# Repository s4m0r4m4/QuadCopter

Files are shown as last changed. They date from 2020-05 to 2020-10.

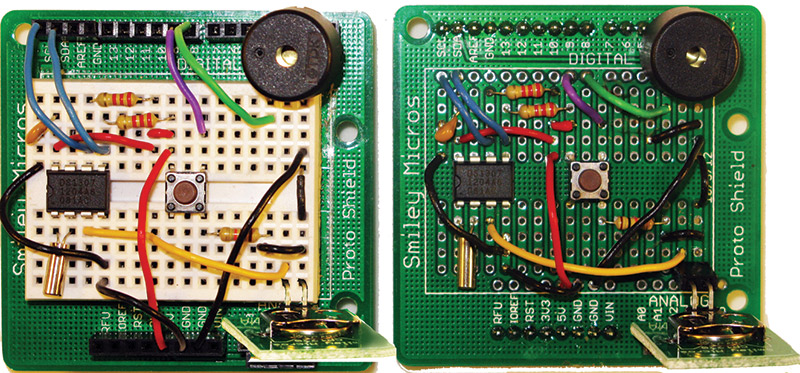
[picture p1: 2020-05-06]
Docs/How to solder.jpg

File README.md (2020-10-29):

# Overview
A simple quadcopter hobby project, build from scratch in terms of both software and hardware.

# Suggested Software Setup
1) Download VS code
2) Install the PlatformIO extension (you can try to beta Arduino Extension, but you will probably have library linking issues)
3) You'll have to install the "Servo" and "SD" libraries using the PlatformIO Extension (use the library panel)
4) It should build!

# Hardware Setup
## MPU-9250
 - VCC ---------------------- 3.3V
 - SDA ----------------------- A4
 - SCL ----------------------- A5
 - GND ---------------------- GND
 - 10 kOhm resistor from 3.3V to SDA
 - 10 kOhm resistor from 3.3V to SCL

Uses code from kriswiner/MPU9250 to read accelerometers, magnetometer, and gyroscopes from MPU9250 and then runs [Magdwick](https://www.x-io.co.uk/res/doc/madgwick_internal_report.pdf) (or Mahoney, depending on how I'm feeling) state estimation algorithm. Big thanks to Kris for his work there.
 
 ## Radio (FlySky FS-CT6) Setup
  TODO: Show pic
  
## Emax MT1806-2280KV Motors:
- https://www.banggood.com/EMAX-MT1806-KV2280-Brushless-Motor-For-Multirotor-p-933931.html?ID=521309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
- Max Trust: 360-460g (depending on propeller)
-	No. of cell: 2-3S
-	Framework: 12N14P
-	Propeller: 5" ~ 6"
-	Length: 26.7mm
-	Shaft: 2mm
- Motor Casing	Diameter: 23mm
-	Weight: 18g

## Battery: 
- http://www.getfpv.com/lumenier-1500mah-3s-45c-lipo-battery.html 
-	Length	88 mm
-	Width	35 mm
-	Height	22 mm
-	Weight	125g
-	C-Rating	45c - Burst 90c
-	Voltage	3s, 11.1v
-	Connector	XT60

## MicroSD Card Reader
- MicroSD card reader for Arduino Uno: https://www.amazon.com/gp/product/B07BJ2P6X6/ref=ppx_yo_dt_b_asin_title_o05_s00?ie=UTF8&psc=1
- MicroSD Card w/ SD-card adapter: https://www.amazon.com/gp/product/B07YLYX4NL/ref=ppx_yo_dt_b_asin_title_o04_s00?ie=UTF8&psc=1
- You can include an SD card reader if you chose to store data while flying (which is a good idea!)
- Since the SD card require a lot of data transfer, you'll get the best performance when connected up to the hardware SPI pins on the Arduino Uno: digital 13 (SCK), 12 (MISO) and 11 (MOSI). You will also need a fourth pin for the 'chip/secondary select' (SS) line. 

## Other Components:
- 5030 propellers: https://www.amazon.com/gp/product/B00Y4QNSFA/ref=oh_aui_detailpage_o00_s01?ie=UTF8&psc=1 
- Arduino Uno R3 (third-party brands are fine too): https://www.amazon.com/gp/product/B00P2FX9WY/ref=oh_aui_detailpage_o00_s03?ie=UTF8&psc=1 
- Frame: FCMODEL X4 M280L Wheelbase Glass Fiber Across Mini Quadcopter Frame Kit DIY RC Multicopter FPV Drone: https://www.amazon.com/gp/product/B014KNMKF0/ref=oh_aui_detailpage_o04_s00?ie=UTF8&psc=1
- Support Legs: https://www.amazon.com/gp/product/B00QHVVKEG/ref=ox_sc_sfl_title_1?ie=UTF8&psc=1&smid=A3Y26MC43SQCQ 
- MPU9250: https://www.amazon.com/Mpu-9250-Nine-axis-Attitude-Acceleration-Magnetic/dp/B00OPNUO9U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 

# Control Analysis
## Controller - Calculating Desired Thrust
Several different controllers were tried out (PD, LQR, and PID). For the moment, I'm trying out the PID. Note that I only present equations about the pitch axis, because the roll axis is symmetric.

We first calculate the pitch and roll errors (be careful to not mix radians and degress!):
- `pitch_error = desired_pitch` (calculated from radio receiver)` - actual_pitch` (calculated from MPU9250)\
- `pitch_rate_error = desired_pitch_rate` (0)` - actual_pitch_rate` (calculated from MPU9250)

And then we keep an estimate of the integral of the pitch and roll errors using a simple rectangular integral estimate:
- `pitch_error_integral = pitch_error_integral + (pitch_error * delta_time)` (where `delta_time` is the time since the last control cycle was ran)

But one issue is integrator windup, where small errors can build up over time to create massive control inputs. To alleviate this problem, I do 2 things - 1) [constrain](https://www.arduino.cc/reference/en/language/functions/math/constrain/) the integrated value to always lie within a certain bound, and 2) add a slow decay term (by multiplying by 0.999 each time):
- `pitch_error_integral = constrain(pitch_error_integral*0.999 + (pitch_error * delta_time), -0.25, 0.25)` (where `delta_time` is the time since the last control cycle was ran)

Then, using the PID control formula, we calculate the desired moment around the roll and pitch axes.

`moment_pitch = (pitch_error * k_P) + (pitch_rate_error * k_D) + (pitch_error_integral * k_I)`

## Mixer - Calculating Propeller Commands from Desired Thrust
First, we need to translate the desired moment around the pitch axis into force requirements from the motor:
- `force_pitch = moment_pitch / (dist * n_motors)`, where `dist` is the distance from the center to each rotor (~95mm) and `n_motors` is the number of motors that can act around that axis (which is 4).

The "force" required for stability is not the only force required from the motor - the motor must also supply enough force to keep the quadcopter aloft. The controller here is not responsible for calculating the force needed to stay aloft, that is left to the operator via the left joystick. Thus, we must "mix" the force from the left joystick with the "delta force" required for stability, to get a final control value to send to the motor:

- `val_motor = f(force_loft + force_stability)`.
In practice, we know the value required for loft (`val_loft`), since that is given by the operator via the left throttle, and the force required for stability using the equations above:
- `f_stability = (+/-)force_pitch + (+/-)force_roll`, where the `+/-` depends on which motor we're talking about in relation to the given axis.

Using the Arduino Servo library, the brushless motors can be commanded with values from 0 (not moving) to 180 (full speed ~15kRPM). In reality, the motor typically starts spinning when a value of ~40 is written to it. To model the thrust of the propeller, we assume the propeller provides full thrust (360g or 3.5N) at full speed and provides 0 thrust at an input of 40 and below. A first-approximation of propeller dynamics teaches us that the thrust provided by a propeller varies quadratically with shaft speed. 

To provide a continuous, non-zero differentiable function (which is needed for the controller), we use a piece-wise function that models the thrust as linear from 0-40 (with a low slope) and then quadratic from 40 to 180. (TODO: add more details)

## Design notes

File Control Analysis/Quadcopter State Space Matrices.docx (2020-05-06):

http://www.electricrcaircraftguy.com/2013/09/propeller-static-dynamic-thrust-equation.html

Simplified A:

0, 00, 0, 0, 00, 01, 00, 1, 0, 00, 0

Simplified B:

[4/(I_θ), 00, 4/(I_φ)][∆F_θ ∆F_φ ]

Where:

[∆F_θ ∆F_φ ]=2*(3.3278*10^(-4) )[∆ω_θ^2 ∆ω_φ^2 ]

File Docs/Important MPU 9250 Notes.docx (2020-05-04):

# Important MPU 9250 Notes

- The slave address of the MPU-9250 is b110100X which is 7 bits long. The LSB bit of the 7 bit address is determined by the logic level on pin AD0. This allows two MPU-9250s to be connected to the same I2C bus. When used in this configuration, the address of the one of the devices should be b1101000 (pin AD0 is logic low) and the address of the other should be b1101001 (pin AD0 is logic high).

# Frequency

Communication with all registers of the device is performed using either I2C at 400kHz or SPI at 1MHz. For applications requiring faster communications, the sensor and interrupt registers may be read using SPI at 20MHz.

Magnetometer normal operating current: 280μA at 8Hz repetition rate

Accelerometer Low Power Mode supports the following output data rates (ODRs): 0.24, 0.49, 0.98, 1.95, 3.91, 7.81, 15.63, 31.25, 62.50, 125, 250, 500Hz.

# Sampling Rates

DLPF = digital low-pass filter

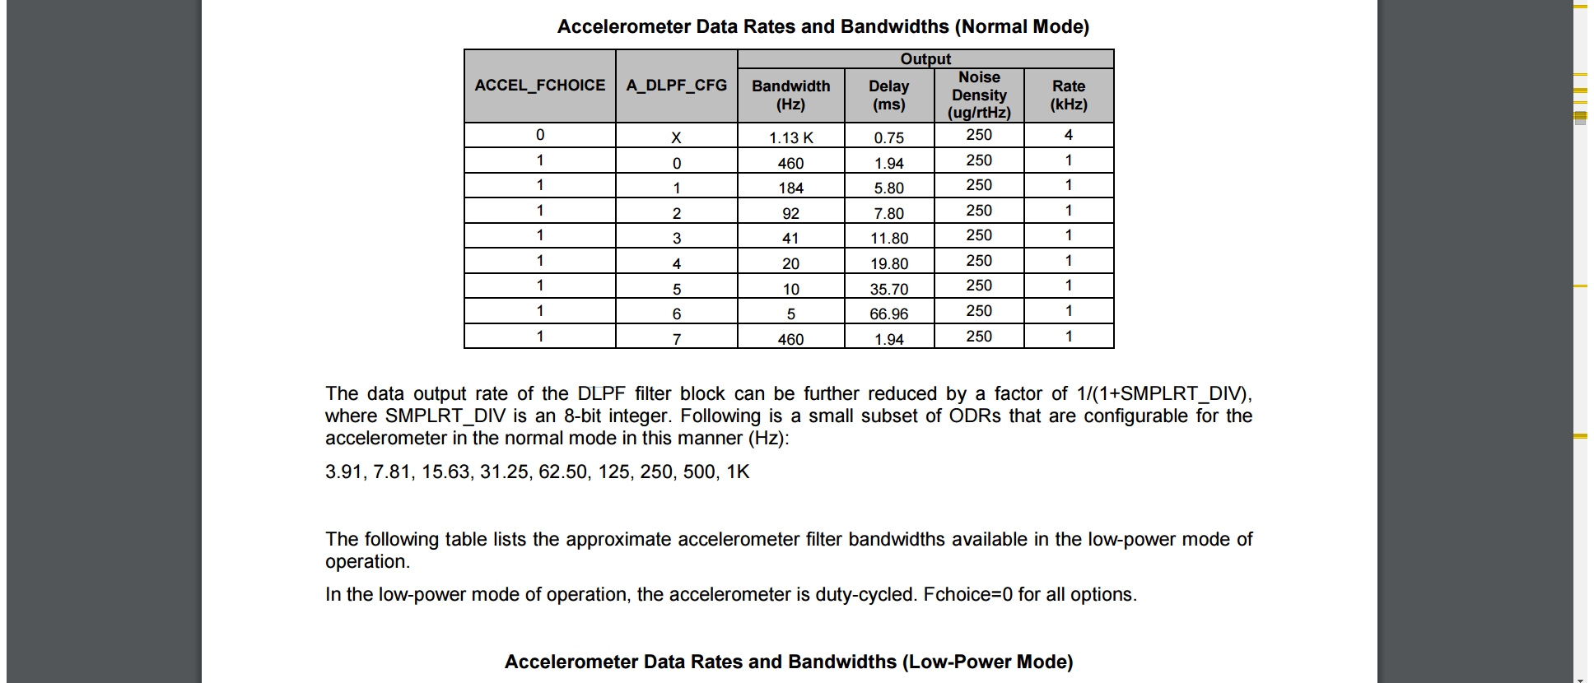
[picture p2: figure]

- A_DLPF_CFG = 3 (BW = 41 Hz) (sampling rate > 82Hz)
- ACCEL_FCHOICE = 1
- Delay = 11.8ms (sampling rate < 84 Hz)

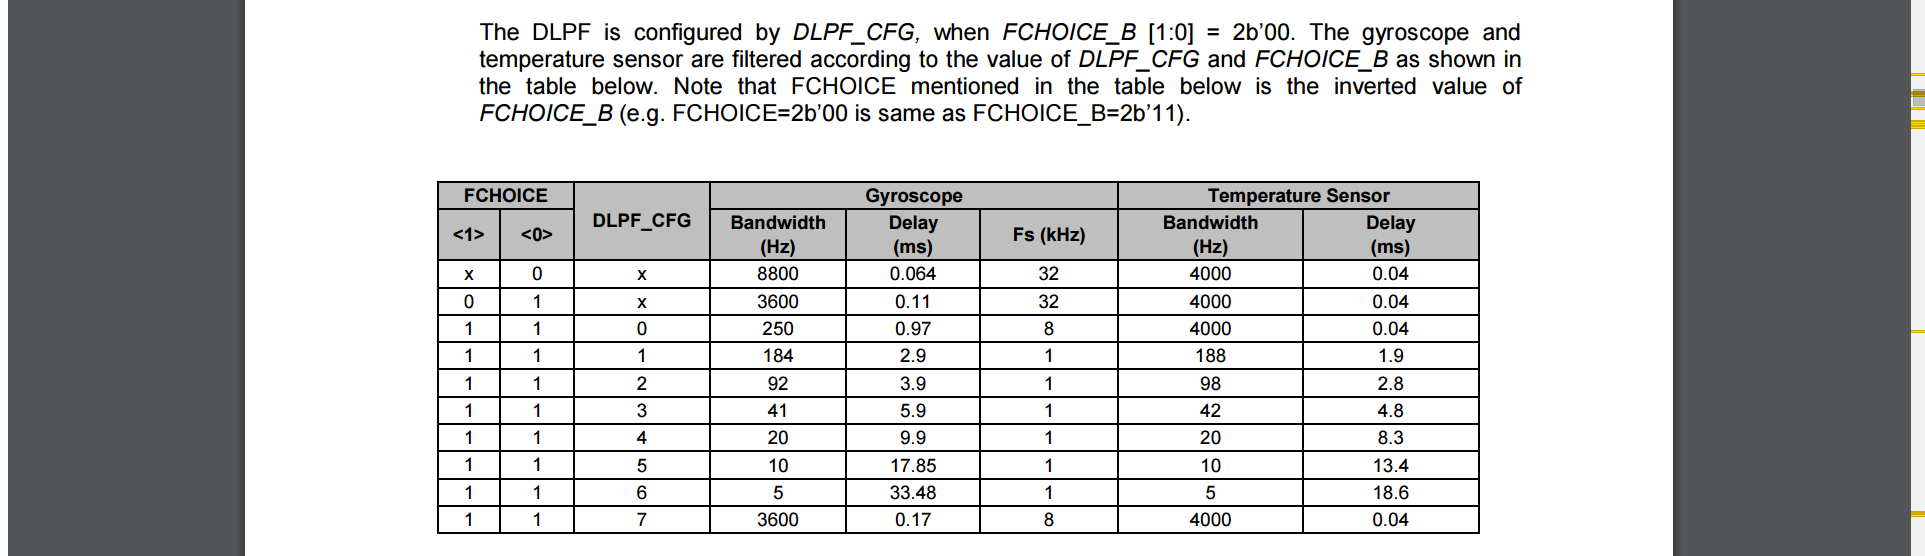
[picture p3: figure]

DLPF_CFG = 3 (41 Hz) (sampling rate > 82 Hz)

FCHOICE = <1><1>

Delay = 5.9ms (sampling rate < 169 Hz)

# Magnetometer

Output data resolution:

- 14-bit (0.6 µT/LSB)
- 16-bit (0.15 µT/LSB)
- Measurement range: ± 4900 µT
- Average current at 8Hz repetition rate: 280µA typ.

AK8963 has the limitation for measurement range that the sum of absolute values of each axis should be smaller than 4912μT.

- |X|+|Y|+|Z| < 4912μT

# I2C Master Clock speed

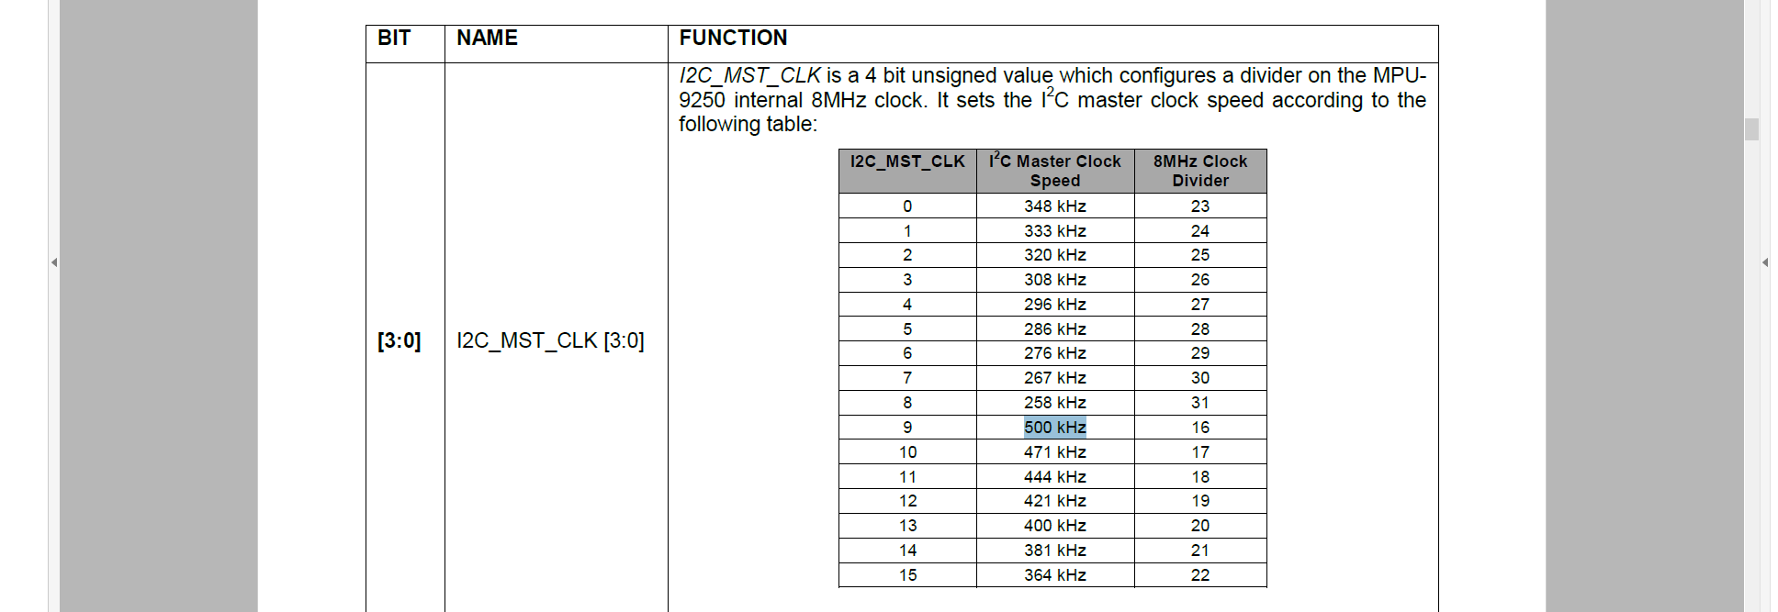
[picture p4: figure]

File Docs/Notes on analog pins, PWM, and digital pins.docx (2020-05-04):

CAN use pulseIn with analog pins (but probably have to filter)

http://electronics.stackexchange.com/questions/67103/can-i-use-the-analog-pins-on-the-arduino-for-my-project-as-digital

Says I can use analog pins as output

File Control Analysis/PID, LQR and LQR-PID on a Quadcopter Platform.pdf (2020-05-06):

# PID, LQR and LQR-PID on a Quadcopter Platform

Lucas M. Argentim
Centro Universitario da FEI ´ unielargentim@fei.edu.br

Willian C. Rezende
Centro Universitario da FEI ´ uniewrezende@fei.edu.br

Paulo E. Santos
Centro Universitario da FEI ´ psantos@fei.edu.br

Renato A. Aguiar
Centro Universitario da FEI ´ preaguiar@fei.edu.br

Abstract—This paper aims to present a comparison between different controllers to be used in a dynamic model of a quadcopter platform. The controllers assumed in this work are an ITAE tuned PID, a classic LQR controller and a PID tuned with a LQR loop. The results were obtained through simulations for 10 different attitudes of the quadcopter, however, in this paper simulation results will be presented for the vertical attitude only (the remainder are analogous and were omitted for brevity).

I. INTRODUCTION

In the last decades the use of Unmanned Aerial Vehicles (UAV) has increased due to the development and improvement of control systems. This increase can also be justified by the fact that these aircrafts are very versatile in contrast to their lower complexity. Within UAV hardware, quadcopters are being widely used for different purposes, such as educational, commercial or entertainment. This choice can be justified by the fact that this model presents a very low moment of inertia and six degrees of freedom, which results in great stability of the quadcopter.
Facing these considerations, the motivation of this work is to develop and compare control mechanisms for a quadcopter model by tuning them with three different approaches. This work applies performance indexes obtained by the ITAE tuning method on a PID controller, a classic LQR controller and a PID controller whose gains where obtained by a LQR loop (according to the method proposed in [1]).
The PID controller was chosen in this work due of its versatility and facile implementation, while also providing a consistent response for the model dynamics attitudes. Also, the LQR controller seemed as a good comparative controller because of its great performance and robustness in the plant in question. The PID controller tuned using a LQR loop is considered since it makes use of the best characteristics of both previous methods.

II. BIBLIOGRAPHIC REVIEW

The scientific literature describes various techniques for controlling quadcopter models in order to perform an efficient stabilising system and navigation. The choice of a suitable technique to be used in a control project depends (among a series of other factors) mainly on the intended use of the quadcopter [2].
Among the most commonly used control techniques, one can cite PID Control [3], Back-Stepping [4], nonlinear H∞ Control [5], Kalman Filter [6] and so on. In this section we provide a brief summary of these control techniques.

There are several controllers already implemented in various models of quadcopters, each one with its peculiarities: in [7] a PID control system is used based on the dynamic model taking into account the bending in the rotor and the propeller. In [8] is presented a backstepping control that uses resources from the Extended Kalman Filter, producing good results in a quadcopter designed for indoor flight.
A comparison of the PID tuning and the Linear Quadratic Regulator (LQR) is proposed in [2] where both controllers have been studied based on a dynamic model of a quadcopter. In this study it is concluded that both controllers provide satisfactory feedback for a quadcopter stabilisation.
Other control strategies were also investigated, such as saturation alignment techniques that were applied to a quadcopter, as described in [9]. [5] describes the H∞ controller, along with a predictive state space controller for a quadcopter performing tracking trajectories tasks.

III. DYNAMIC MODEL
The mathematical model of the quadcopter has to describe its attitude according to the well-known geometry of this UAV. More specifically, this aerial vehicle basically consists of four propellers located orthogonally along the body frame. Figure 1 shows this configuration.

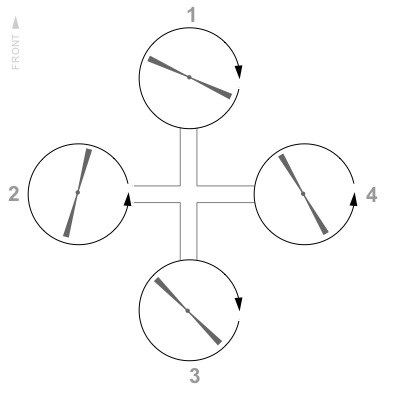
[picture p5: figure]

Fig. 1. Plant view of the Quadcopter

There are three movements that describe all possible combinations of attitude Figure 2 : Roll (rotation around the X axis) is obtained when the balance of rotors 2 and 4 is changed (speed increases or decreases). By changing the φ angle, lateral acceleration is obtained; pitch movement (rotation around the Y axis) is obtained when the balance of the speed of the rotors 1 and 3 is changed. The θ angle change results in a longitudinal acceleration; yaw (ψ) (rotation about the Z axis) is obtained by a simultaneous change of speed of the pair (1,3) or (2,4).

978-1-4799-0400-6/13/$31.00 ©2013 IEEE

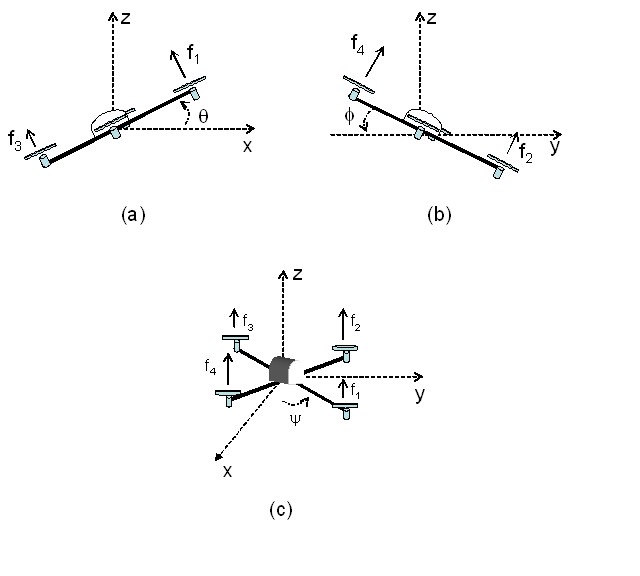
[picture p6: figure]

Fig. 2. Description of the Roll(φ), Pitch (θ) and Yaw (ψ) angles

Due to the presence of two coordinate systems, it is necessary to use the transformation matrix to obtain the response of any movement from a coordinate system (Earth-fixed frame) to the other (model-fixed frame). With 6 degrees of freedom, modelling can be a complex task. The equations and the parameters needed to generate the matrices that describe the Quadcopter attitudes are estimated based on empirical experimentations and measurements of a LinkQuad Quadcopter¹ .
This work assumes the physical model presented in [10] as described below.
A. Vertical attitude equations

The equations that describe the vertical attitudes related to the Z axis of the aircraft are shown below. The state space matrices that make up these attitudes are described in equations 1 through 5:

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
+ 7BU

(1)

Y =

z w Ω1 | Ω2 | Ω3 | Ω4

T

(2)

where,

1From UAS Technologies Sweden AB (http://www.uastech.com/).

A =

0 1 | 0 | 0 | 0 | 0
0 0 −0.0106 0.0106 −0.0106 0.0106
0 0 | −10 | 0 | 0 | 0
0 0 | 0 | −10 | 0 | 0
0 0 | 0 | 0 | −10 | 0
0 0 | 0 | 0 | 0 | −10

(3)

B =

0 0 1 −1 1 −1

T

(4)

C =

0 1 0 0 0 0.

(5)

In equation 1, z is the vertical coordinate in Earth-fixed frame, w is the vertical speed in body-fixed frame and Ωn is the angular rate of each propeller. It is possible to modify the values of the matrix C so either the vertical speed or position are chosen as the system output.

IV. CONTROL TECHNIQUES
After analysing the transfer function from the state space matrices, it was noticed that in most attitudes the equations could be simplified. Some of the roots from the numerator (zeros) could be simplified with the corresponding roots of the denominator (poles). By doing this, it was possible to obtain a lower-order plant model, which means that the controller gains could be calculated in a straightforward way. This controller (tuned with simplified equations) was able to give a consistent response when used in the original plant, as seen in the results shown in the following sections.
A. LQR - Linear Quadratic Regulator
A generic form of the system presented in equation 1 is shown in equation 6 where x˙ and x represent the system outputs and inputs respectively. The matrices A and B were also described in equations 3 and 4 and represent the particular dynamic model of the quadcopter LinkQuad [10].
x˙ = Ax + Bu | (6)

According to [11] for a Linear Quadratic Regulator Controller tuning it is convenient to know a vector u that minimises the quadratic cost function presented in equation 7 which leads to the linear control law presented in equation 8.

J =

Z ∞

0

(x.Qx + u.ru)dt | (7)
u = −Kx | (8)

Therefore the vector K described in equation 8 need to be set in order to minimise equation 7, and for this reason the parameters k, p, e were obtained applying a lqr function shown in equation 9, where Q is a square matrix of sixth order described in equation 10, adjusted to provide the most efficient values and R is a unitary vector.

[k, p, e] = lqr(A, B, Q, R) | (9)

Q =

10000000 0 0 0 0 0
0 | 1 0 0 0 0
0 | 0 1 0 0 0
0 | 0 0 1 0 0
0 | 0 0 0 1 0
0 | 0 0 0 0 1

(10)

The output of the LQR function was the vector K shown in equation (11) containing the six elements that controls each state of the system individually, this makes a expansion of the state space function necessary. This expansion is obtained solving the equation 6 and the result is a system of six equations 12 to 17 that represent each one of the states.

K =

−3.1623 × 10³
−1.5070 × 10³
1.3062
−1.3062
1.3062
−1.3062

(11)

x˙1 = x2 | (12)
x˙2 = −0.0106x3 − 0.0106x4 + 0.0106x5 + 0.0106x6 | (13)
x˙3 = 10x3 + 7u | (14)
x˙4 = 10x4 + 7u | (15)
x˙5 = 10x5 + 7u | (16)
x˙6 = 10x6 + 7u | (17)

When a block diagram of the new expanded equations 12 to 17 is built, and the control law shown in equation 8 is applied, it becomes a closed loop system with six feedback gains and no inputs. As the regulators are known for leading the responses of the system to a null value, a disturbance (step) was performed at the state which the control was required and a result for the vertical position is presented in figure 3.

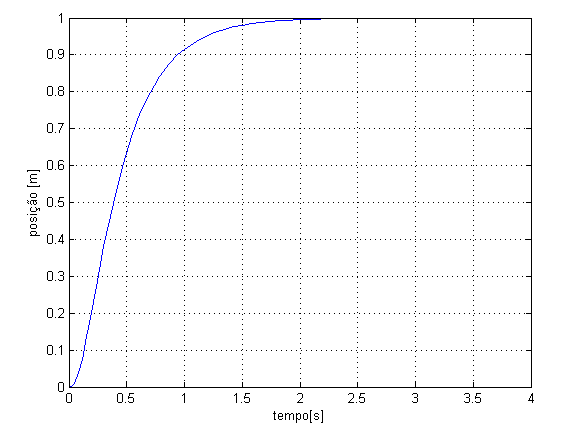
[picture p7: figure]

Fig. 3. Vertical position step response for LQR control

Figure 3 shows the step response for the vertical position of the plant with no overshooting value and with an accommodating time of two seconds. It was also performed the LQR control for all other movements of the quadcopter from where analogous satisfactory results were obtained.
Figure 4 shows the vertical-speed step response that was acquired when a step source was placed in the vertical position state.

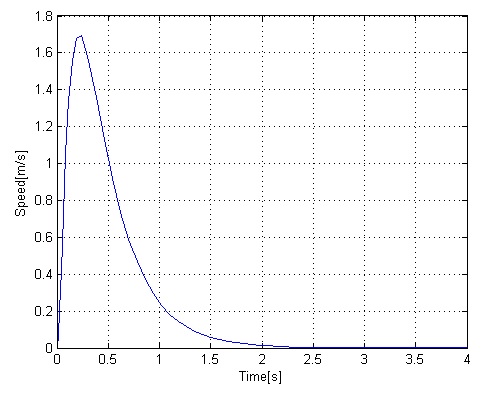
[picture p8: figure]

Fig. 4. Vertical speed step response for LQR Control

As mentioned above, the speed response is null after a transition time because of the regulator controller. It does not mean that in a practical model the vertical speed goes to zero because there will always be a disturbance at the position state.

B. ITAE - tuning PID
1) Vertical speed controller: The simplified transfer function that describes the vertical position is shown in equation 18:
Gw(s) = −0.0424
s(s + 10) | (18)

Once obtained the transfer function of the attitude, a controller function can be defined as:

C(s) = (k3s

2 + k1s + k2)
s
, | (19)

where k3, k2, k1 represents, respectively, the derivative, integral and proportional gains. Then, the transfer function of the closed-loop system can be dened as:

Fw(s) = | k3s

2 + k1s + k2
s

3 + (10 + k3)s

2 + k1s + k2

. (20)

Equalling the coefficients of the characteristic equation 20 with ITAE model optimum coefficients [12], values k1, k2 and k3 were obtained.

k1 = 860 | (21)
k2 = 8000 | (22)
k3 = 25 | (23)

After implementing the controller using the values found with the ITAE method, it was verified that the plant was not being controlled. That can be explained analysing the behaviour of the model, which tends to a negative response before achieving stability. This kind of process usually has its origin on two competing effects: a fast dynamic effect and a slow dynamic effect. These effects produce the negative start to the response before the step recovers to settle at a positive state value. To solve this problem, an additional negative unitary gain is placed at the output of the controller to maintain a negative feedback loop, which gives us a reverseacting controller.
The phase delay compensators are also known for their properties of assisting for a better steady response with the consequence of shifting the poles to the right side of the root locus plane. This effect causes a destabilisation of the model and a longer transient time feedback [13]. Analysing the transfer function of the plant, it is possible to perceive the natural presence of one integrator, so the integral gain k2, shown in equation 22 was set to null.
Equations 21 and 23 (k1 and k3 gains) were applied in the ways mentioned above, producing the response shown at figure 5.

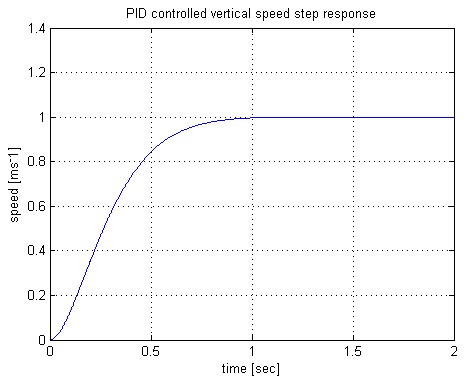
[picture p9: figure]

Fig. 5. PID vertical speed step response.

Figure 5 shows the step response for the vertical speed controlled by the gains calculated above. Equations 21 and 23 (respectively k1 and k3 gains) were obtained using the simplified model shown in equation 18 and later applied to the space state matrices given by equations 3 through 5.

2) Vertical position controller: The transfer function of vertical position is described by equation 24, which will be controlled by new proportional, integral and differential gains: Gz(s) = −0.0424
s
2(s + 10). | (24)

The new vertical position controller CB can be described as
CB(s) = (k3B)s

2 + (k1B)s + (k2B)
s
. | (25)

Considering the same simplification shown in equation 18, and neglecting k2B for the same reason as k2 22 , the vertical position transfer function was obtained, as shown in equation 26.

Fz(s) = | CB(s)(k3s

2 + k1s)
s(1 + CB(s)((k3 + 1)s

2 + (k1 + 10)s)) (26)

Performing an analogous process to that described in Section IV-B1 for equation 26, the new gains k1B, k2B and k3B are
k1B = 63.92 | (27)
k2B = 31.39 | (28)
k3B = 0.7 | (29)

Applying this new controller to the state space matrices given by equations 3, 4 and the modified equation 5 (to select the vertical positions as the system output), we obtained the response illustrated in figure 6. Once again, the model simplification was validated.

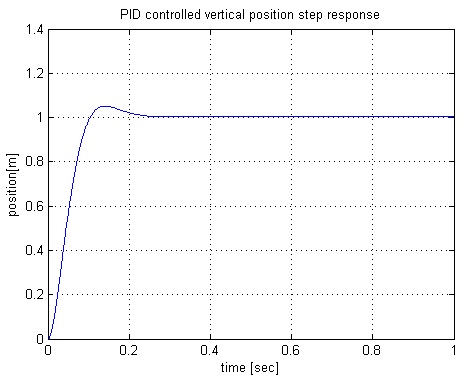
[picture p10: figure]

Fig. 6. PID Vertical position step response.

C. LQR - tuning PID
1) Vertical speed controller: As a comparative criterion, we decided to tune controllers for the same attitudes, but this time using the method proposed by [1], where the PID gains are calculated based on equations 30 trhough 34
Kp Kd
= KpC

−1
(30)
Ki = (Im + KdCB)Ki | (31)

Where:

C =

C
CA − CBKp
(32)

Kp = (Im + KdCB)

−1
(KpC + KdCA) (33)

Ki = (Im + KdCB)

−1Ki | (34)

The methodology for obtaining the PID parameters is fully described in [1]. For better tuning results, it is necessary to execute the algorithm innumerous times until the desired response for the system is reached. In order to accomplish that, an algorithm was developed 2
that calculates automatically the gains based on the simplified space state matrices generated from equation 18 of the plant and the matrix Q (from the LQR control theory). Development time increased drastically and the controller could be tuned with reasonable parameters for the system.
Using matrix Q = diag[0, 10000, 10000] as a parameter of our algorithm, the following gains kP w, kIw and kDw were obtained:

kP w = −2.3758 × 10³
(35)
kIw = −1 | (36)
kDw = −173.6511 | (37)

Figure 7 shows the step response for the vertical speed controller.

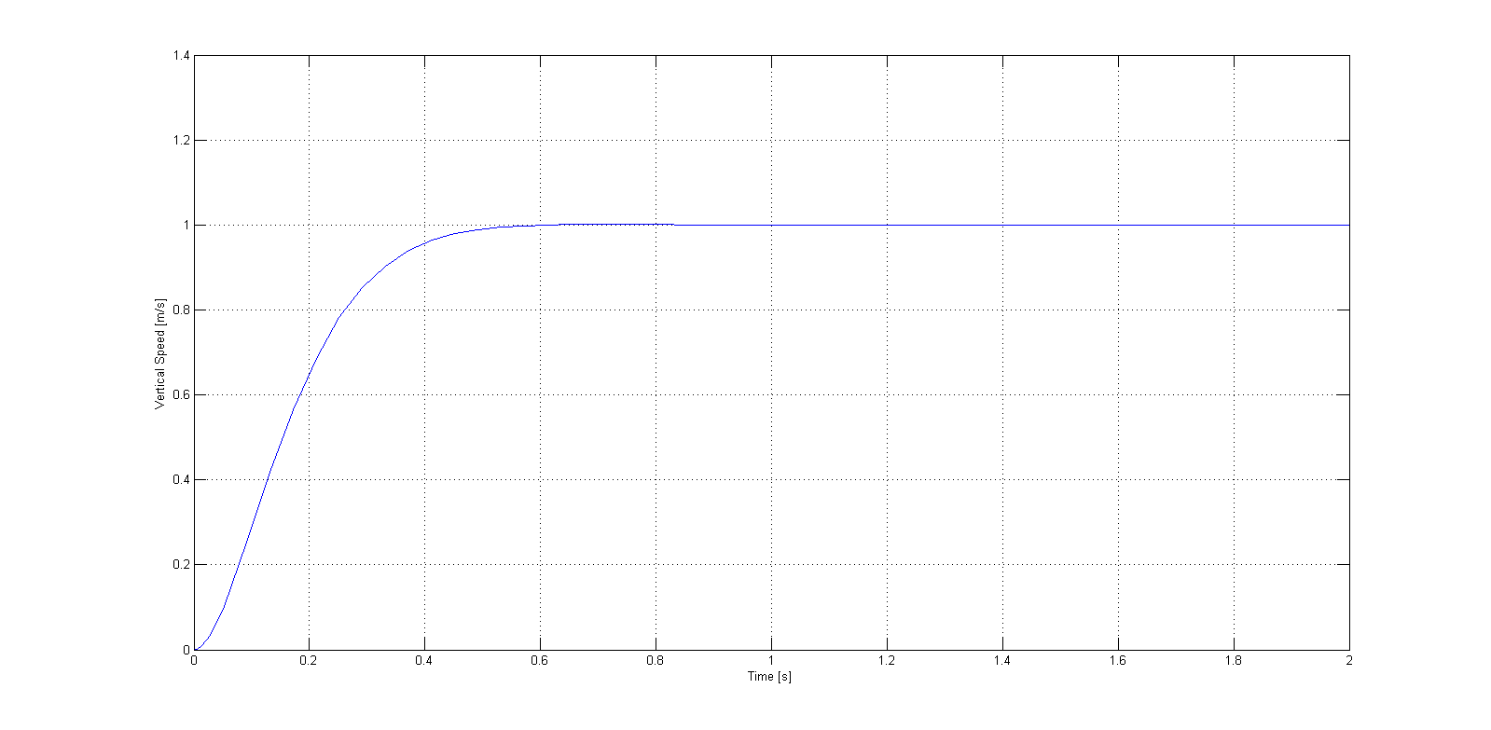
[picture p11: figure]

Fig. 7. PID - LQR vertical speed step response

2Available at: https : //dl.dropbox.com/u/9185049/P ID LQ.m

2) Vertical position controller: Analogously, the same methodology can be applied for the vertical position controller, by using the state space matrices given by equation 24. Using matrix Q = diag[0, 0, 1000, 10000] as parameter for the software, the parameters kP z, kIz and kDz are as follows:
kP z = −834.6291 | (38)
kIz = −1 | (39)
kDz = −701.7901 | (40)

Figure 8 shows the step response for the vertical position controller.

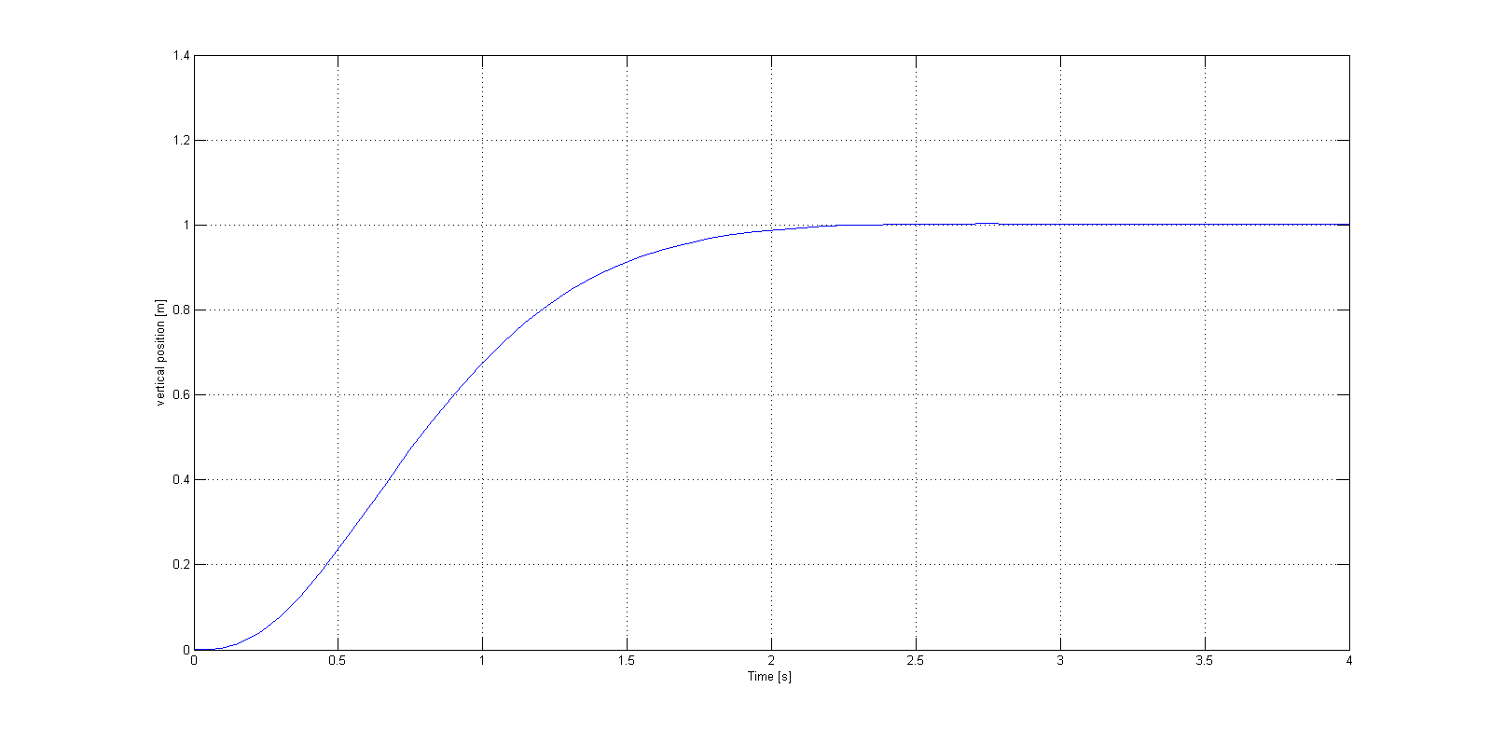
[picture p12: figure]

Fig. 8. PID - LQR vertical position step response.

V. RESULT ANALYSIS

Looking back at the step responses shown above, it is clear that each control system has a different response for the same attitudes. However, it is possible to choose the most suitable technique based on the characteristics that is needed for the quadcopter.

A. Vertical speed responses

Comparing figures 4, 5 and 7, it is possible to notice that the PID controller tuned by LQR theory is the fastest. The controller presented a fast response with no overshooting value.

B. Vertical position responses

The results for the vertical position controllers presented some differences between their performances. The PID controller tuned with ITAE performance indexes, presented in figure 6, showed a faster response compared to the other controllers. Even with less than ten percent overshooting, the settling time is around 0.25 seconds.
When looking at the step response for the PID tuned with LQR theory (figure 8) and the classic LQR (figure 3) , the settling time is about the same, but with no overshoot value. However, it is important to point out that the robustness of the controllers are not being analysed. Faster controllers does not necessarily means consistent responses under disturbances.

C. Instability in longitudinal attitudes

The authors judged important to expose the fact that the longitudinal movements (speed and position) presents a natural instability. It is clear when analysing the root locus diagram that there is a complex pole pair in the right half of the s-plane.

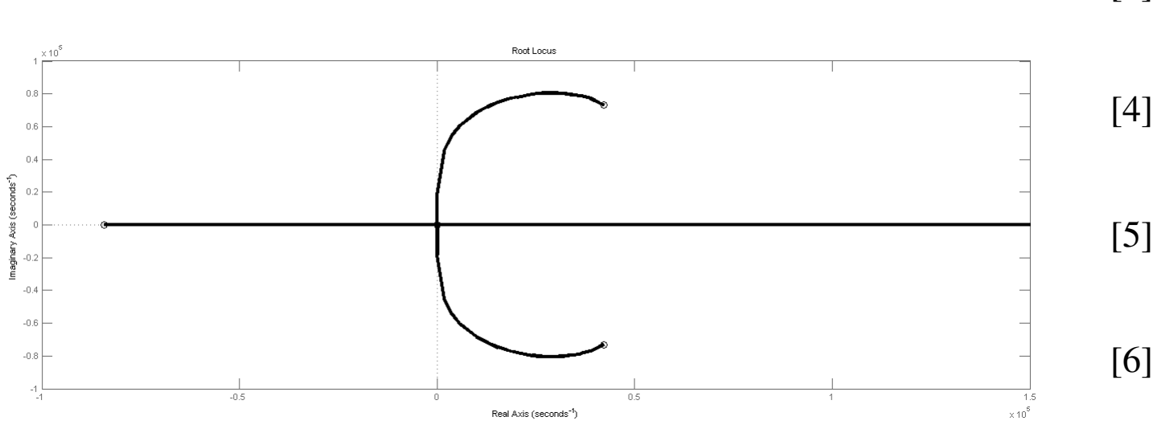
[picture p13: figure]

Fig. 9. Root Locus for longitudinal speed

Using a method for pole allocation by a state feedback loop [14], stability is achieved. However, this method implies that all states described in the equations of the attitude are accessible (usually the angular rates of the motors, speed and position of the frame). If that is not the case, a state observer is proposed as a practical solution. The methodology applied to the problem can be extended to the longitudinal position controller in an analogous way.

VI. CONCLUSION

Considering the previous analysis and results found in this work it is easy to observe that the plant was controlled with three different control methods presenting satisfactory results. Each one of these controllers offers singular characteristics that makes hard to say which one is the best.
It is known that the LQR controllers are robust and produce a very low steady state error, but with a big transition delay and using six feedback gains, that makes them a bad choice when the system needs fast parameters update and has no direct access to all states of the plant. On the other hand, a PID controller gives a faster response but not with robust gains as the previous controller. The classic PID theory implies in not developing a robust controller.
Looking back at the responses we verified that in some attitudes, the PID tuned by the LQR controller presented inferior performance when compared to the others. However, this delayed response does not compromise the correct operation of the plant in the tested conditions. Therefore, as a practical solution, the classic PID tuned by an LQR robust controller resulted in a robust, versatile and easy implementable controller. In future work, the results will be applied in a LinkQuad quadcopter recently obtained, which will allow us to make considerations about the actual applicability of the controllers proposed, while also assessing the robustness of the methods.

Acknowledgements This work has been partially sponsored by FAPESP project 2012/04089-3.

REFERENCES

[1] S. Mukhopadhyay, “PID equivalent of optimal regulator,” Electronics Letters, vol. 14, no. 25, pp. 821–822, 1978.
[2] S. Bouabdallah, A. Noth, and R. Siegwart, “PID vs LQ control techniques applied to an indoor micro quadrotor,” in proceedings of IEEE International Conference on Intelligent Robots and Systems IROS, 2004, pp. 2451–2456.
[3] A. L. Salih, M. Moghavvemi, H. A. F. Mohamed, and K. S. Gaeid, “Flight PID controller design for a UAV quadrotor,” Scientific Research and Essays, vol. 5, pp. 3360–3367, 2010.
[4] T. Madani and A. Benallegue, “Backstepping control for a quadrotor helicopter,” Intelligent Robots and Systems, 2006 IEEE/RSJ International Conference on, pp. 3255–3260, 2006.
[5] G. V. Raffo, M. G. Ortega, and F. R. Rubio, “An integral predictive/nonlinear H infinity control structure for a quadrotor helicopter,” Automatica, vol. 46, pp. 29–39, 2009.
[6] M. Jun, S. I. Roumeliotis, and G. S. Sukhatme, “State estimation of an autonomous helicopter using Kalman filtering,” in Intelligent Robots and Systems, 1999, pp. 1346 – 1353.
[7] P. P. R. Mahony and P. Corke, “Modelling and control of a quadrotor robot,” in In Proceedings Australasian Conference on Robotics and Automation, 2006.
[8] A. Soumelidis, P. Gaspar, G. Regula, and B. Lantos, “Control of an experimental mini quad-rotor UAV,” in proceedings of 16th Mediterranean Conference on Control and Automation, 2008, pp. 1252–1257.
[9] J. Escareo and S. Salazar-Cruz, “Embedded control of a four-rotor UAV,” in Proceedings of the 2006 american control conference, 2006, pp. 3936–3941.
[10] T. Jirinec, “Stabilization and control of unmanned quadcopter,” Master’s thesis, CZECH TECHNICAL UNIVERSITY IN PRAGUE, 2011.
[11] K. Ogata, Modern Control Engineering. Prentice Hall - Br, 1999.
[12] R. H. B. Richard C. Dorf, Modern Control Systems. Addison-Wesley, 1995.
[13] R. D. H. Charles L. Phillips, Basic Feedback Control Systems, 1990.
[14] J. Kautsky, N. Nichols, and P. V. Dooren, “Robust pole assignment in linear state feedback,” International Journal of Control, vol. 41, pp. 1129–1155, 1985.

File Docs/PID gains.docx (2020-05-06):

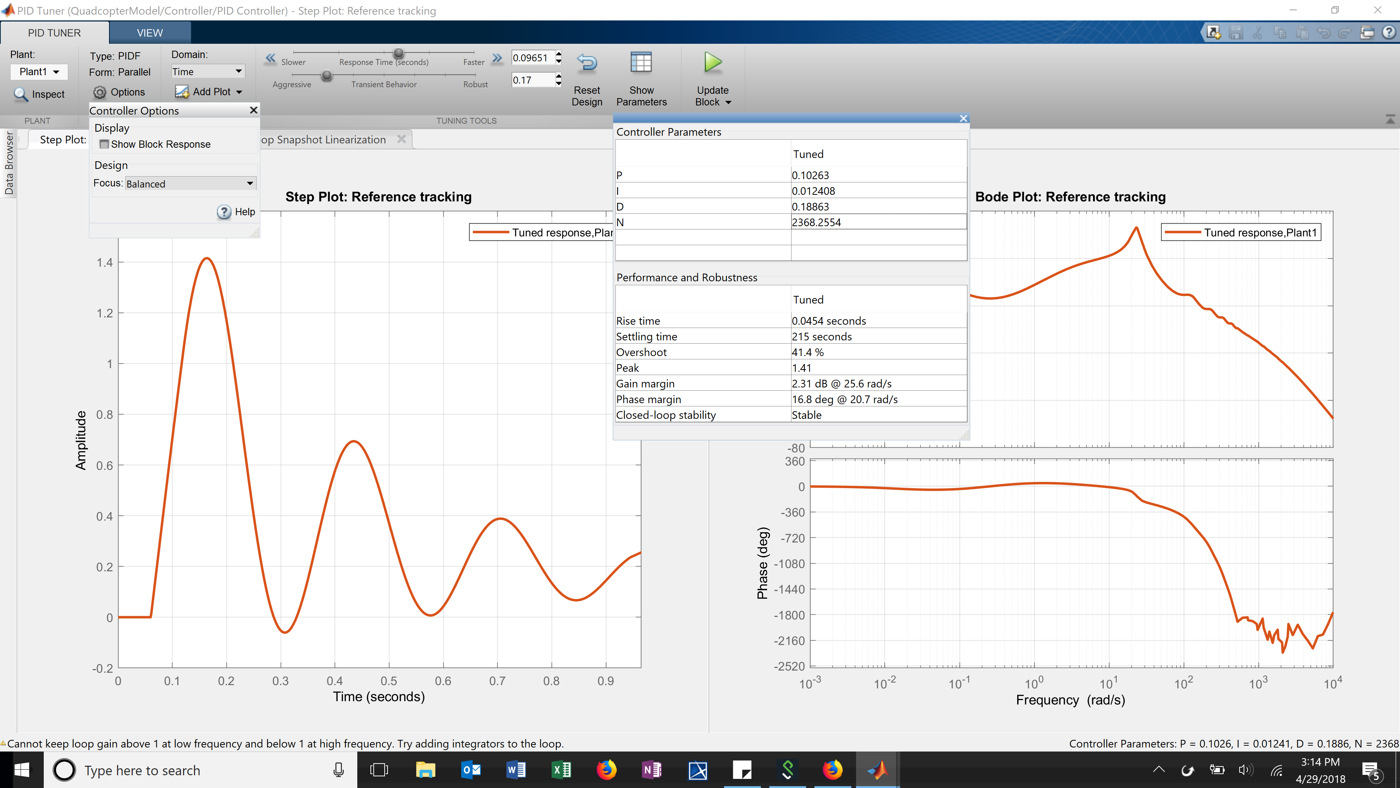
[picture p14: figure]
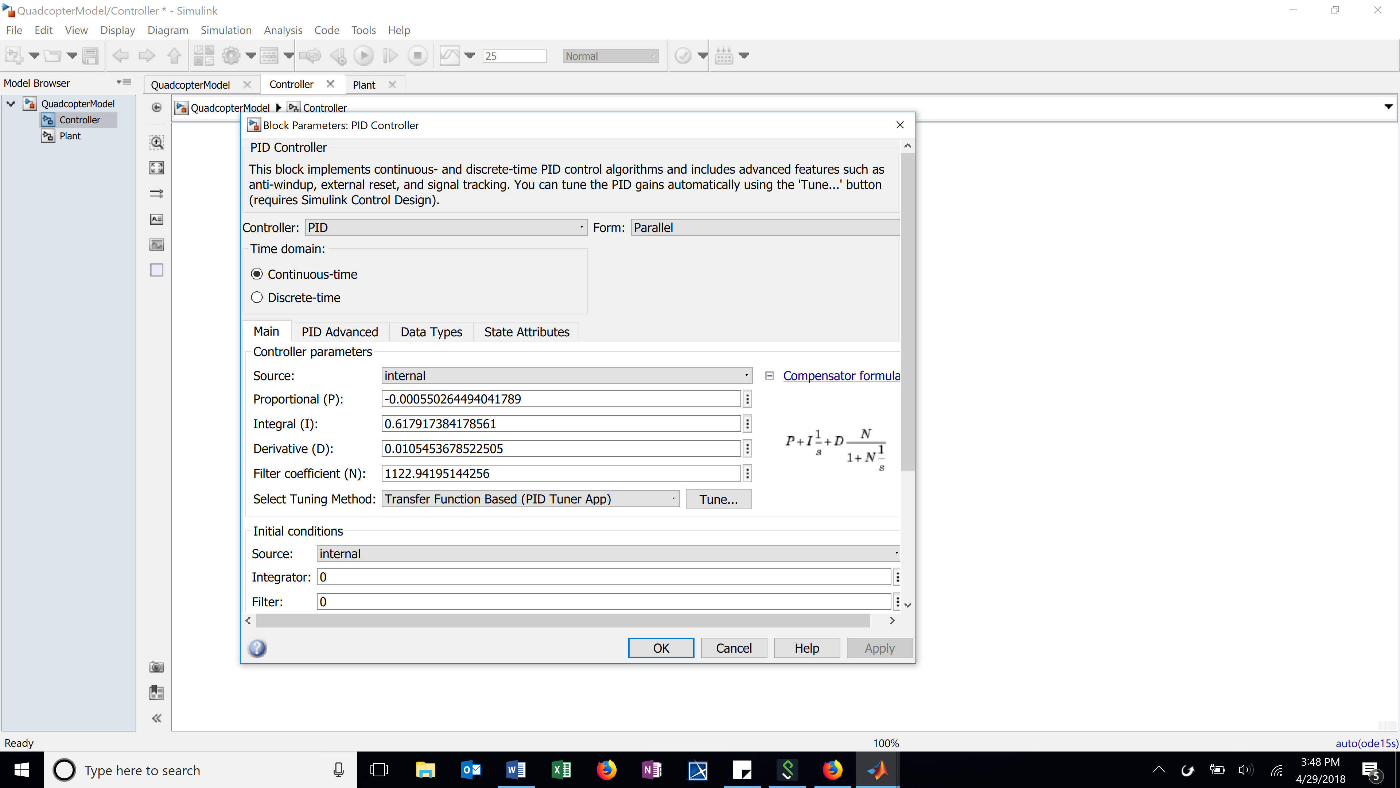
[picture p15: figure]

Best so far!!!

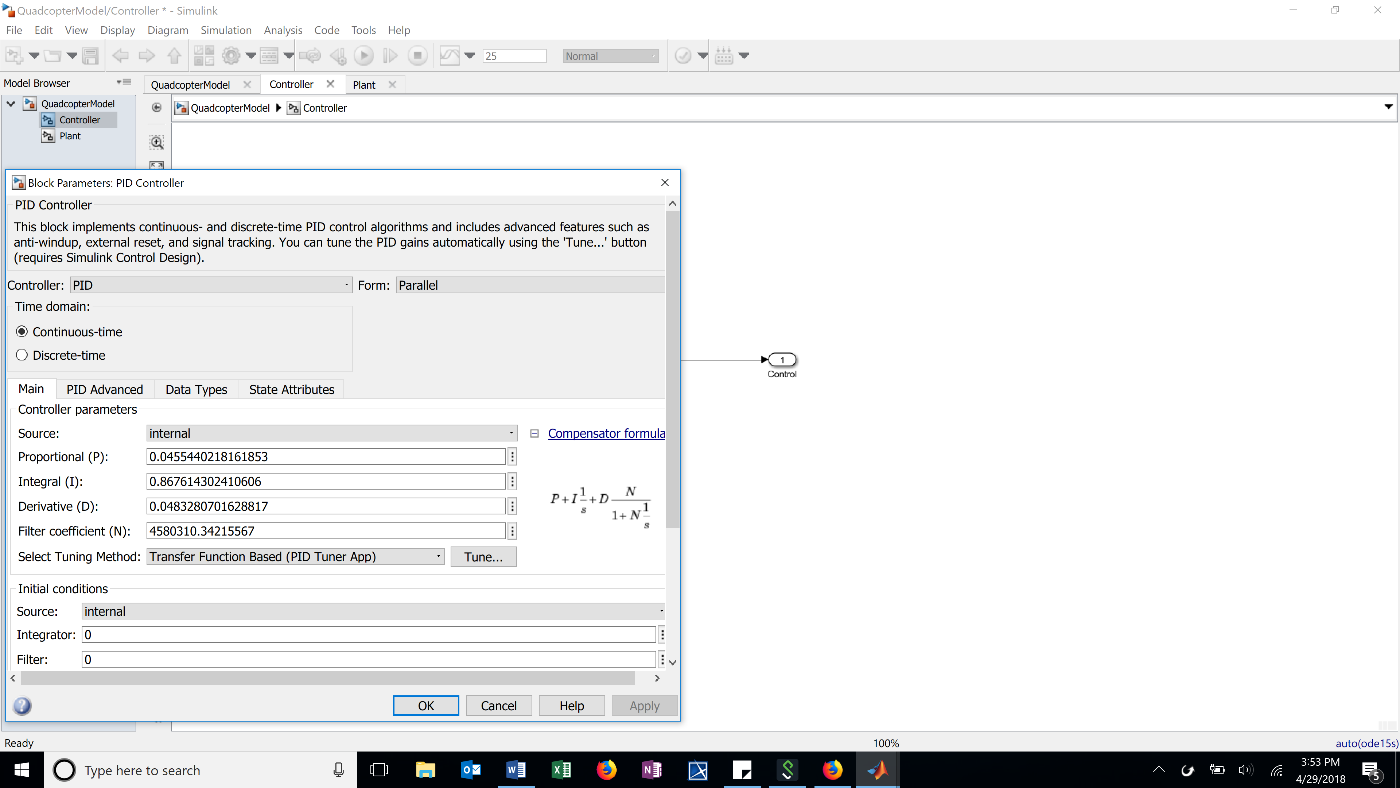
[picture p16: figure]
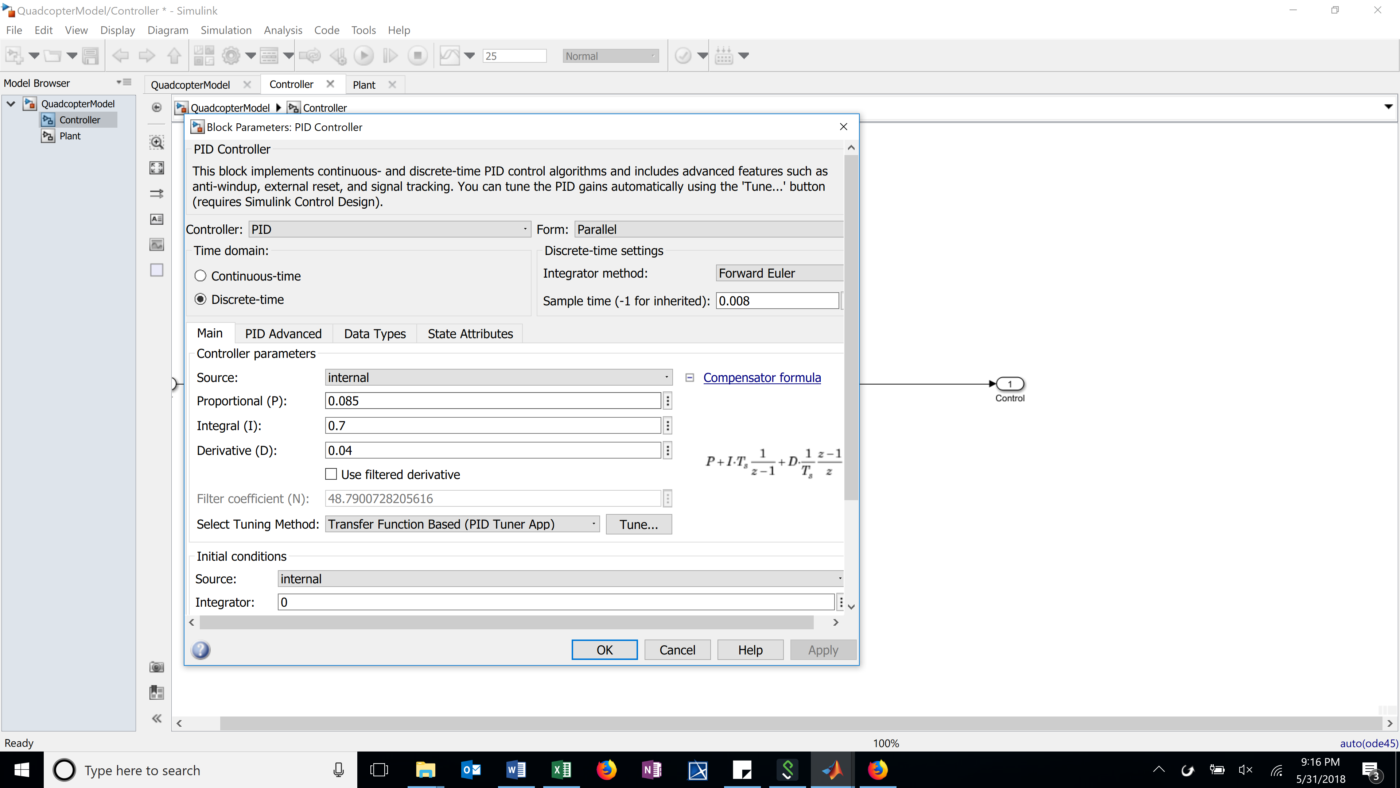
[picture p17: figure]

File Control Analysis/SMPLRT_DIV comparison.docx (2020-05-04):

SMPLRT_DIV = 0x07

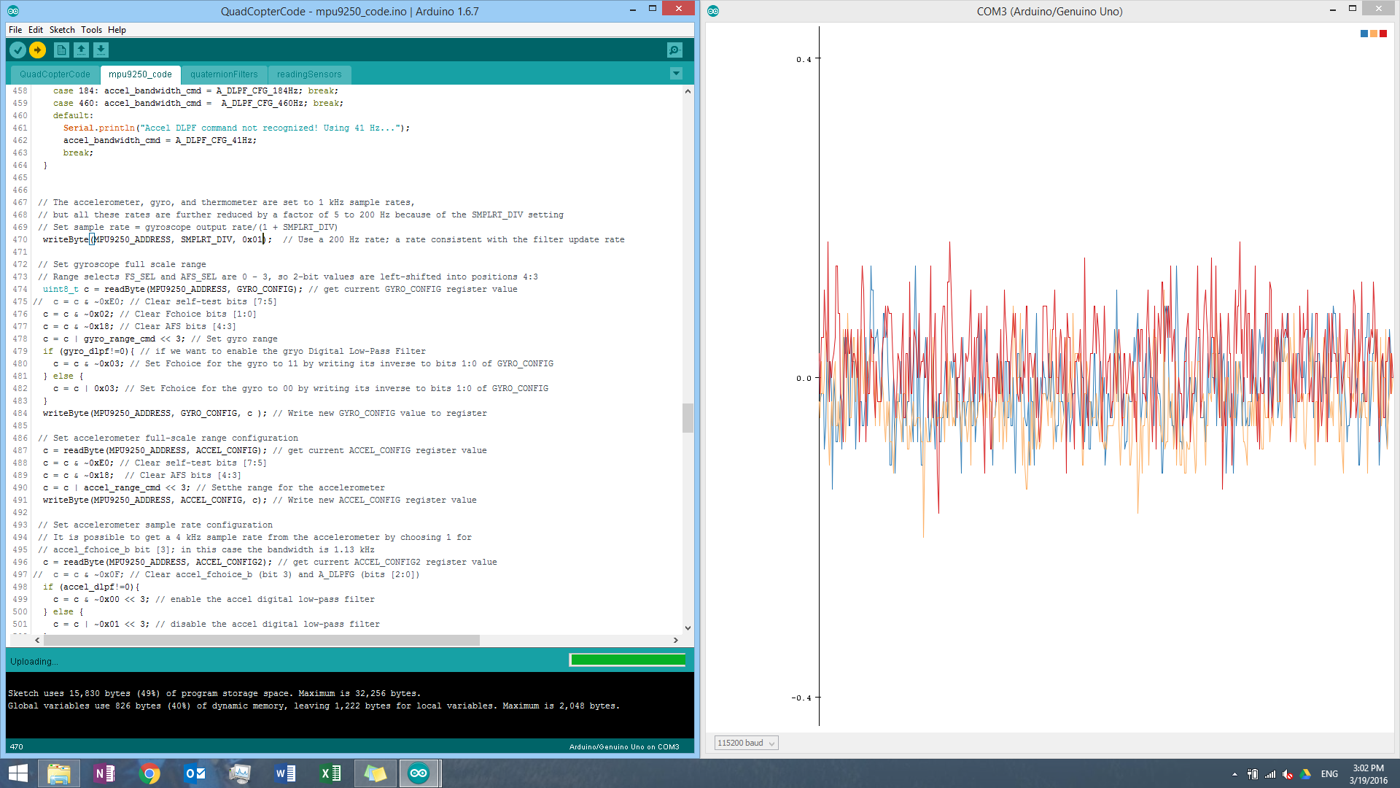
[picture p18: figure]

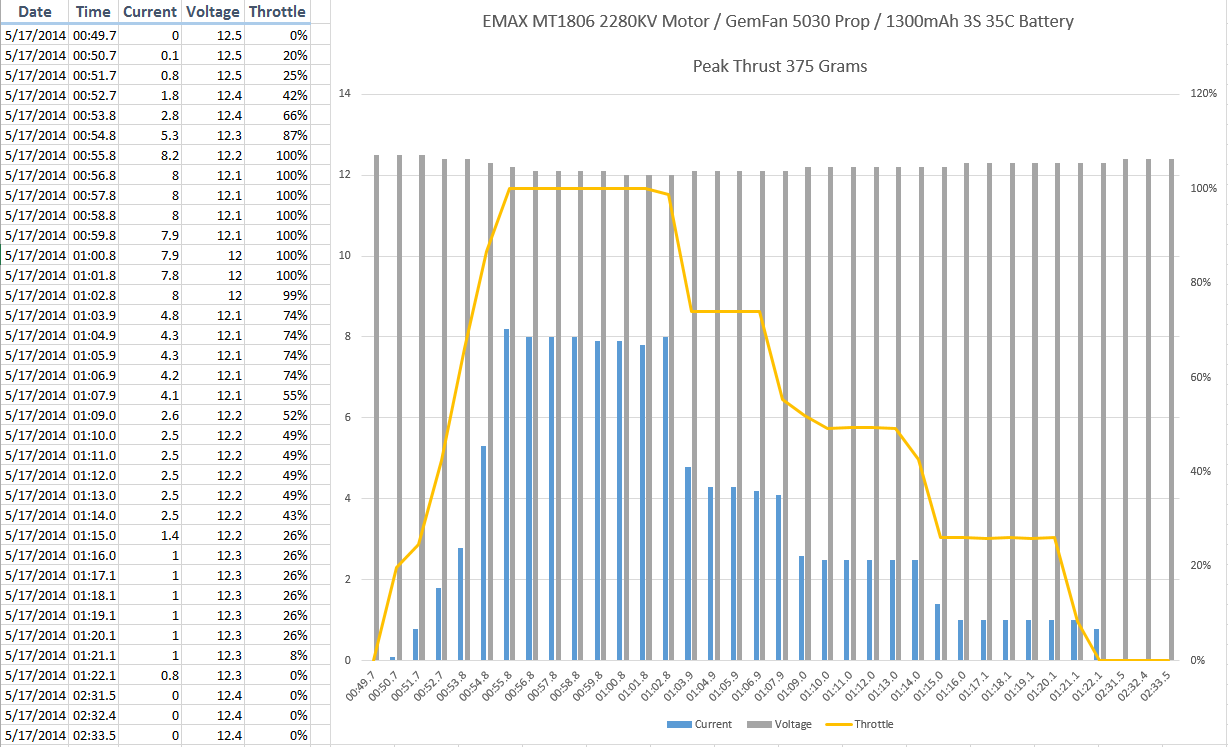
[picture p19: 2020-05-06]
Docs/5030 Propellar with EMAX Motor Thrust Profile.png

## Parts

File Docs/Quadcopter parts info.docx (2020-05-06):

# Quadcopter Frame

- FCMODEL X4 M280L Wheelbase Glass Fiber Across Mini Quadcopter Frame Kit DIY RC Multicopter FPV Drone (https://www.amazon.com/gp/product/B014KNMKF0/ref=oh_aui_detailpage_o04_s00?ie=UTF8&psc=1)
- Weight about: 156g →
  - 55 g per side (x2)
  - 24g /24 connectors = 1 g
  - 10 g per top plate
  - 10 g /4 big connectors = 2.5 g

# Legs

- https://www.amazon.com/gp/product/B00QHVVKEG/ref=ox_sc_sfl_title_1?ie=UTF8&psc=1&smid=A3Y26MC43SQCQ
- Height:150mm.
- Weight:18g/pcs

# MPU-9250

- https://www.amazon.com/Mpu-9250-Nine-axis-Attitude-Acceleration-Magnetic/dp/B00OPNUO9U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
- 0.106 ounces (3 g)

# Propellers

- https://www.amazon.com/gp/product/B00Y4QNSFA/ref=oh_aui_detailpage_o00_s01?ie=UTF8&psc=1
- 5030
- Weight: 4.5g / pcs

https://www.amazon.com/gp/product/B00P2FX9WY/ref=oh_aui_detailpage_o00_s03?ie=UTF8&psc=1

# Arduino

- https://www.amazon.com/gp/product/B00P2FX9WY/ref=oh_aui_detailpage_o00_s03?ie=UTF8&psc=1
- 0.3 ounces (9 g)

# Electric Motors

- Emax MT1806 2280KV
- KV: 2280
- Max Trust: 460g
- No. of cell: 2-3S
- Framework: 12N14P
- Propeller: 5" ~ 6"
- Length: 26.7mm
- Shaft: 2mm
- Diameter: 23mm
- Weight: 18g
- Wires: 9g?

Prop Volts Throttle Amps Watts RPM Thrust (g)
6030 11.1 30% 1.7 12.58 8191 106
6030 11.1 50% 2.8 20.72 9818 155
6030 11.1 65% 3.8 28.12 11186 206
6030 11.1 85% 6.5 48.1 13643 309
6030 11.1 100% 8 59.2 14618 355
6045 11.1 30% 1.9 21.09 7104 115
6045 11.1 50% 3.2 35.52 8574 170
6045 11.1 65% 4.8 53.28 10022 232
6045 11.1 85% 8 88.8 11882 328
6045 11.1 100% 9.7 107.67 12692 370

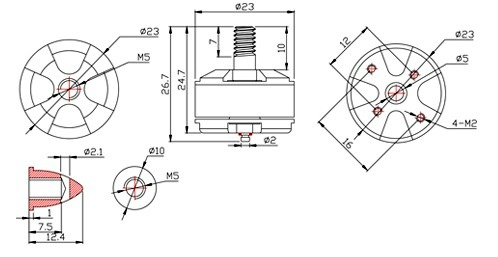
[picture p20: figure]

ESCs

__0_000_______________10_000________.______",_000_______________

# Batts

- http://www.getfpv.com/lumenier-1500mah-3s-45c-lipo-battery.html

Length | 88 mm
Width | 35 mm
Height | 22 mm
Weight | 125g
C-Rating | 45c - Burst 90c
Voltage | 3s, 11.1v
Connector | XT60

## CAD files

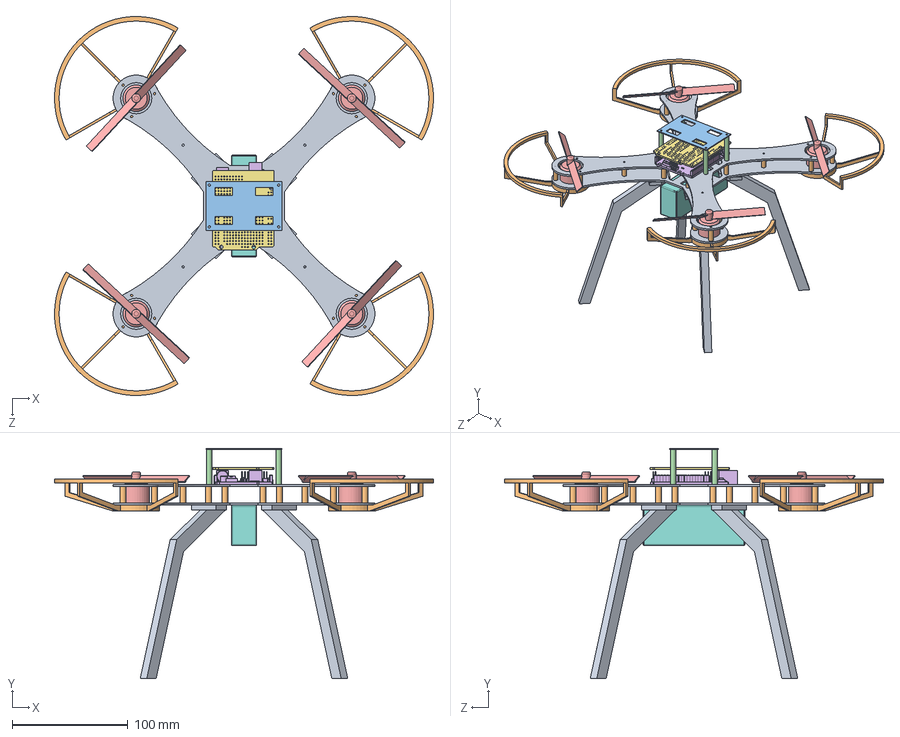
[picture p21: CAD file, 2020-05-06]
Control Analysis/Solid Model Calcs/QuadCopterSolidModel v1/QuadCopter v1/FULL Assembly v1.SLDASM
327.4 x 198.8 x 327.4 mm
Frame Bottom x 2
Short Spacer x 24
Top Plate
Long Spacer x 4
Motor with Propeller x 4
Arduino uno
Arduino proto shield R3
Battery
Leg x 4
Propeller Guard x 4

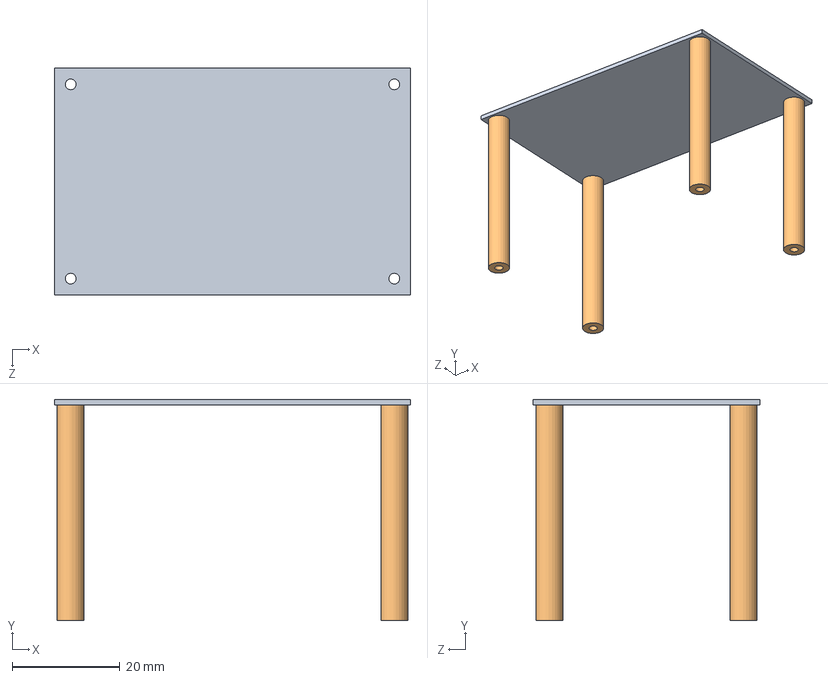
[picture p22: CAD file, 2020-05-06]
Control Analysis/Solid Model Calcs/QuadCopterSolidModel v1/Top Assembly.SLDASM
66.0 x 41.0 x 42.0 mm
Top Plate
Long Spacer x 4

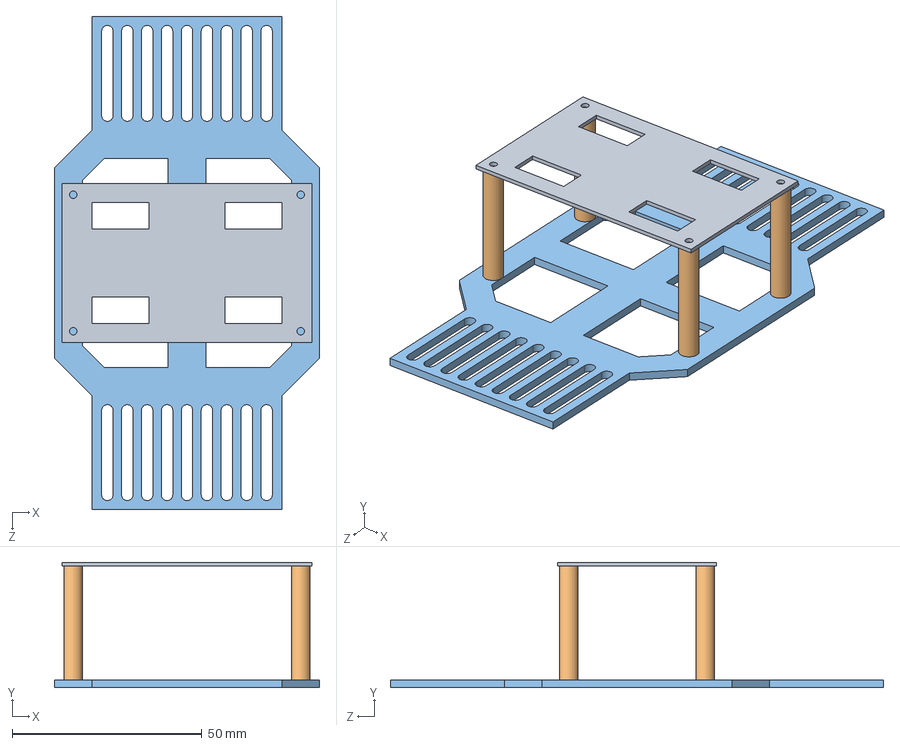
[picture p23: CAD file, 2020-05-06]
Control Analysis/Solid Model Calcs/QuadcopterSolidModel v2/Top Assembly.SLDASM
70.0 x 33.0 x 130.0 mm
Top Plate
Long Spacer x 4
Frame Top

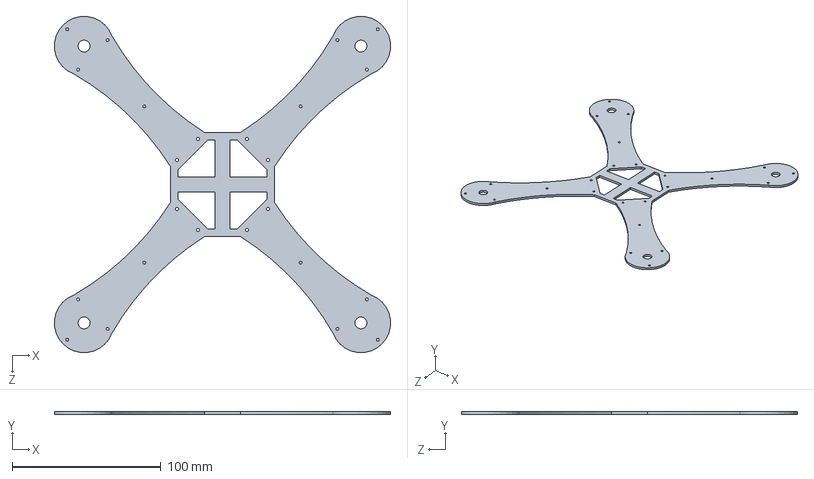
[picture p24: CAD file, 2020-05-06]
Control Analysis/Solid Model Calcs/QuadCopterSolidModel v1/QuadCopter v1/Frame Bottom.SLDPRT
226.0 x 2.00 x 226.0 mm

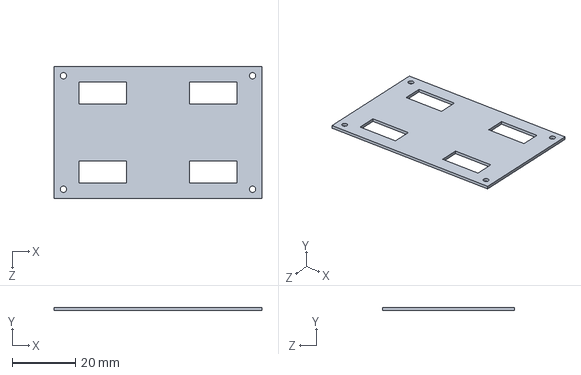
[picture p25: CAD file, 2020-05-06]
Control Analysis/Solid Model Calcs/QuadCopterSolidModel v1/Top Plate.SLDPRT
66.0 x 1.00 x 42.0 mm

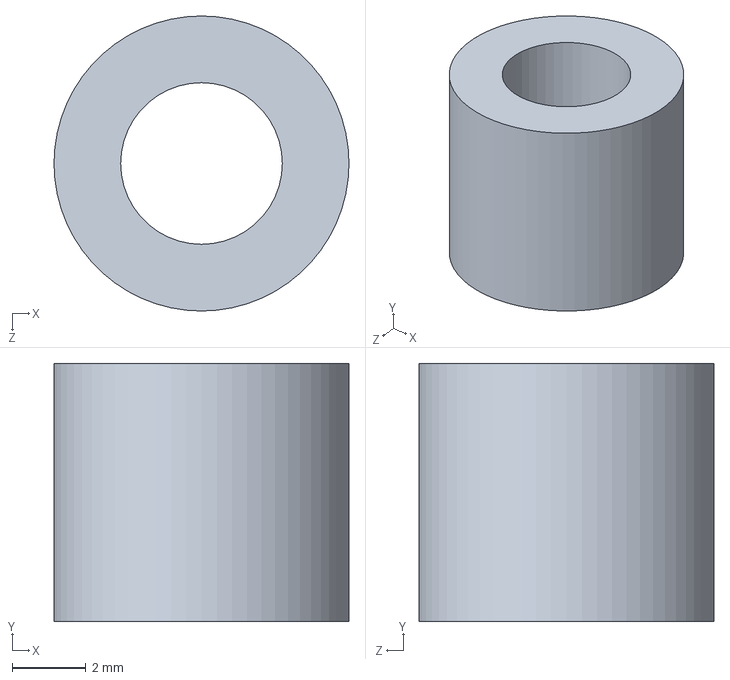
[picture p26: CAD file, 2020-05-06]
Control Analysis/Solid Model Calcs/QuadcopterSolidModel v2/Battery plate spacer.SLDPRT
8.00 x 7.00 x 8.00 mm

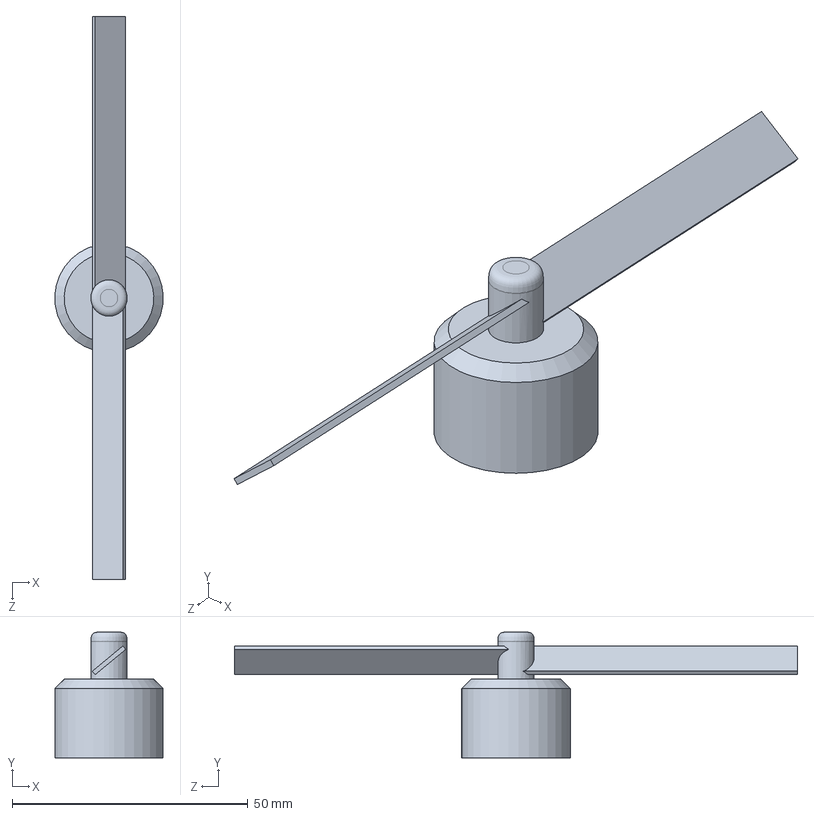
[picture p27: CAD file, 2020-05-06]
Control Analysis/Solid Model Calcs/QuadCopterSolidModel v1/Motor with Propeller.SLDPRT
23.0 x 26.7 x 119.4 mm

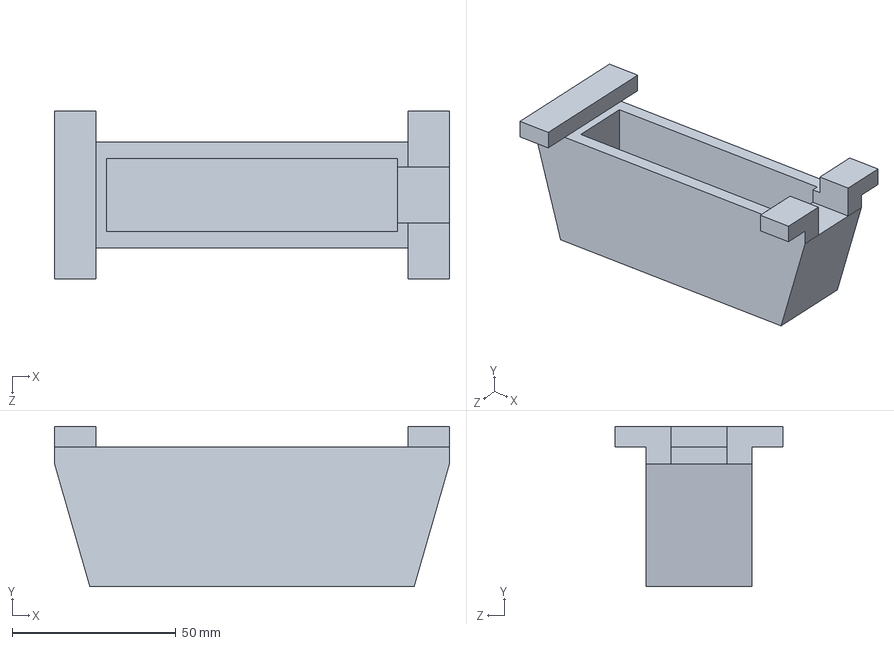
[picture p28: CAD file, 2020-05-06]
Control Analysis/Solid Model Calcs/QuadCopterSolidModel v1/QuadCopter v1/Battery Case for Printing.SLDPRT
120.6 x 48.9 x 51.4 mm

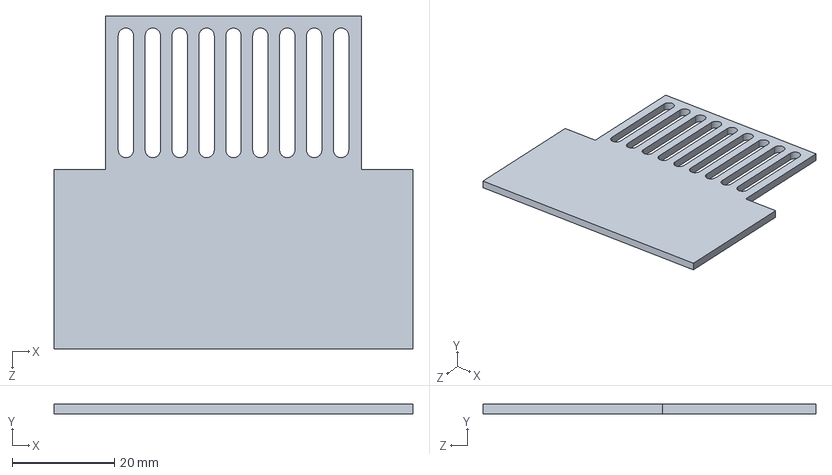
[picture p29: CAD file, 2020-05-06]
Control Analysis/Solid Model Calcs/QuadCopterSolidModel v1/Frame Top.SLDPRT
70.0 x 2.00 x 65.0 mm

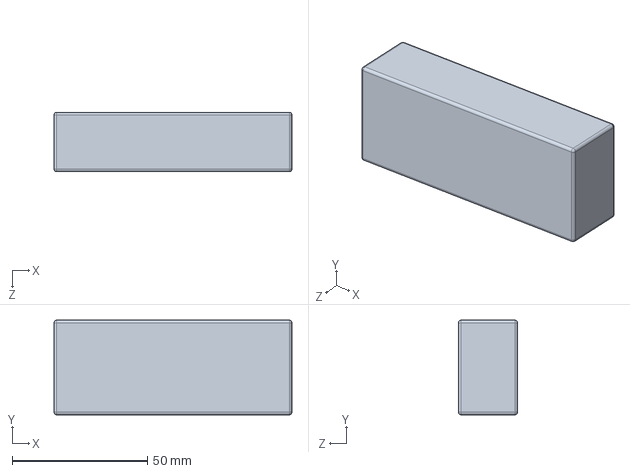
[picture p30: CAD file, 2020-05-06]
Control Analysis/Solid Model Calcs/QuadcopterSolidModel v2/Battery.SLDPRT
88.0 x 35.0 x 22.0 mm

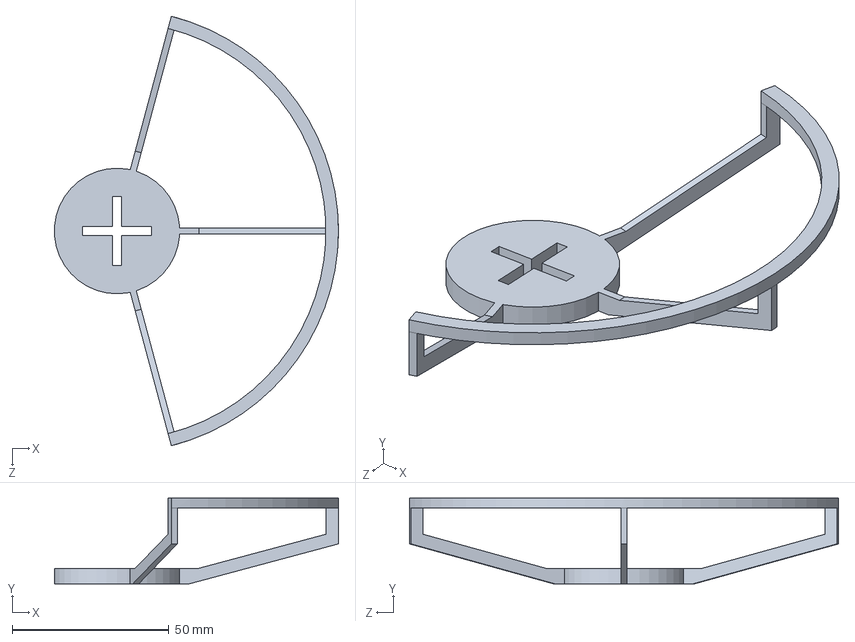
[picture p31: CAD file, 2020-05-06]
Control Analysis/Solid Model Calcs/QuadCopterSolidModel v1/QuadCopter v1/Propeller Guard.SLDPRT
90.5 x 27.4 x 136.9 mm

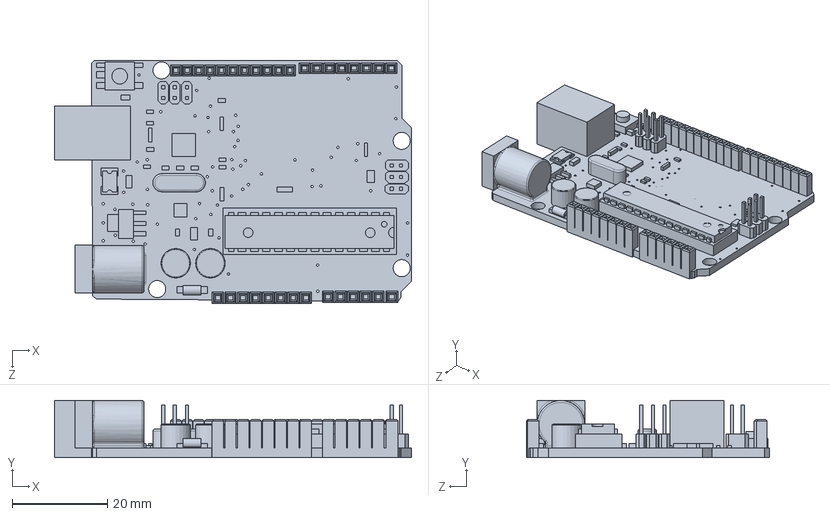
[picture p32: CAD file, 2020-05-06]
Control Analysis/Solid Model Calcs/QuadcopterSolidModel v2/Arduino uno.SLDPRT
75.0 x 12.0 x 51.0 mm

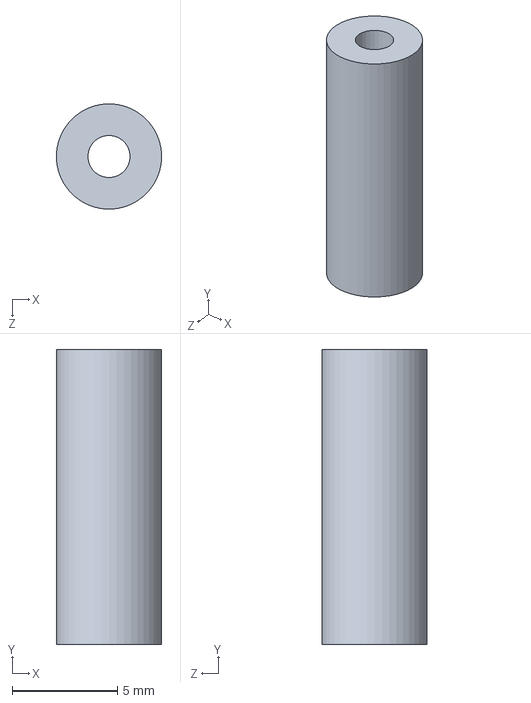
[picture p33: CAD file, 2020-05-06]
Control Analysis/Solid Model Calcs/QuadCopterSolidModel v1/QuadCopter v1/Short Spacer.SLDPRT
5.00 x 14.0 x 5.00 mm

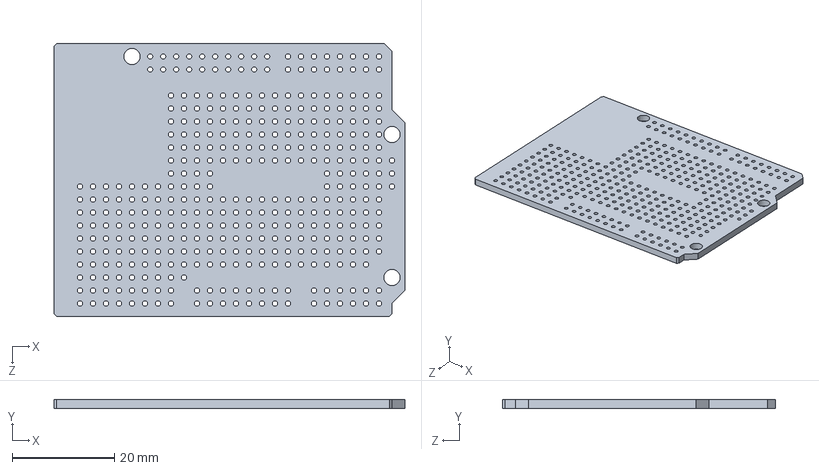
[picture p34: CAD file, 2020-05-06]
Control Analysis/Solid Model Calcs/QuadcopterSolidModel v2/Arduino proto shield R3.SLDPRT
68.6 x 1.70 x 53.3 mm

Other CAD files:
Control Analysis/Solid Model Calcs/QuadcopterSolidModel v2/Top Plate.SLDPRT
Control Analysis/Solid Model Calcs/QuadCopterSolidModel v1/Arduino proto shield R3.SLDPRT
Control Analysis/Solid Model Calcs/QuadCopterSolidModel v1/Arduino uno.SLDPRT
Control Analysis/Solid Model Calcs/QuadCopterSolidModel v1/Leg.SLDPRT
Control Analysis/Solid Model Calcs/QuadCopterSolidModel v1/Long Spacer.SLDPRT
Control Analysis/Solid Model Calcs/QuadCopterSolidModel v1/QuadCopter v1/Arduino proto shield R3.SLDPRT
Control Analysis/Solid Model Calcs/QuadCopterSolidModel v1/QuadCopter v1/Arduino uno.SLDPRT
Control Analysis/Solid Model Calcs/QuadCopterSolidModel v1/QuadCopter v1/Leg.SLDPRT
Control Analysis/Solid Model Calcs/QuadCopterSolidModel v1/QuadCopter v1/Long Spacer.SLDPRT
Control Analysis/Solid Model Calcs/QuadcopterSolidModel v2/Bottom battery Plate.SLDPRT
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

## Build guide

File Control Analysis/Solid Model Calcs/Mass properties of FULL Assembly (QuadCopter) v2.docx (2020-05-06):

# Mass Props with Correct Coord System (v2)

Mass properties of FULL Assembly

Configuration: Default

Coordinate system: -- default --

Mass = 479.82 grams

Volume = 269511.90 cubic millimeters

Surface area = 172278.66 square millimeters

Center of mass: ( millimeters )

X = -0.10

Y = -35.71

Z = 0.03

Principal axes of inertia and principal moments of inertia: ( grams * square millimeters )

Taken at the center of mass.

Ix = (-0.01, 0.00, 1.00) Px = 2167333.57

Iy = ( 1.00, 0.00, 0.01) Py = 2256755.58

Iz = ( 0.00, 1.00, 0.00) Pz = 3399475.06

Moments of inertia: ( grams * square millimeters )

Taken at the center of mass and aligned with the output coordinate system.

Lxx = 2256750.28 Lxy = -1031.22 Lxz = -746.55

Lyx = -1031.22 Lyy = 3399474.11 Lyz = 165.40

Lzx = -746.55 Lzy = 165.40 Lzz = 2167339.83

Moments of inertia: ( grams * square millimeters )

Taken at the output coordinate system.

Ixx = 2868456.42 Ixy = 653.99 Ixz = -748.04

Iyx = 653.99 Iyy = 3399479.22 Iyz = -373.05

Izx = -748.04 Izy = -373.05 Izz = 2779050.14

One or more components have overridden mass properties:

Top Plate<1><Default>@Top Assembly<1><Default>

Long Spacer<1><Default>@Top Assembly<1><Default>

Long Spacer<2><Default>@Top Assembly<1><Default>

Long Spacer<3><Default>@Top Assembly<1><Default>

Long Spacer<4><Default>@Top Assembly<1><Default>

Frame Arm<1><Default>

Arduino uno<1><Predeterminado>@Arduino Assembly<1><Default>

Arduino proto shield R3<1><Default>@Arduino Assembly<1><Default>

Battery<1><Default>

Motor with Propeller<1><Default>

Leg<1><Default>

Propeller Guard<1><Default>

Frame Arm<2><Default>

Frame Arm<3><Default>

Frame Arm<4><Default>

Propeller Guard<5><Default>

Propeller Guard<6><Default>

Propeller Guard<7><Default>

Motor with Propeller<8><Default>

Motor with Propeller<9><Default>

Motor with Propeller<10><Default>

Leg<5><Default>

Leg<6><Default>

Leg<7><Default>

Battery plate spacer<1><Default>

Battery plate spacer<2><Default>

Battery plate spacer<3><Default>

Battery plate spacer<4><Default>

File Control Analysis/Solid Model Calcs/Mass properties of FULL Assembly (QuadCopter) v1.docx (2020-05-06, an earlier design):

# Mass Props with Correct Coordinate System

Mass properties of FULL Assembly

Configuration: Default

Coordinate system: -- default --

Mass = 491.60 grams

Volume = 305080.41 cubic millimeters

Surface area = 204341.56 square millimeters

Center of mass: ( millimeters )

X = -0.04

Y = -29.29

Z = 0.02

Principal axes of inertia and principal moments of inertia: ( grams * square millimeters )

Taken at the center of mass.

Ix = ( 0.00, 0.00, 1.00) Px = 2623253.84

Iy = ( 1.00, 0.00, 0.00) Py = 2693637.59

Iz = ( 0.00, 1.00, 0.00) Pz = 4263586.34

Moments of inertia: ( grams * square millimeters )

Taken at the center of mass and aligned with the output coordinate system.

Lxx = 2693636.60 Lxy = -540.75 Lxz = -287.46

Lyx = -540.75 Lyy = 4263586.10 Lyz = 314.27

Lzx = -287.46 Lzy = 314.27 Lzz = 2623255.07

Moments of inertia: ( grams * square millimeters )

Taken at the output coordinate system.

Ixx = 3115393.09 Ixy = -11.29 Ixz = -287.87

Iyx = -11.29 Iyy = 4263587.01 Iyz = -11.81

Izx = -287.87 Izy = -11.81 Izz = 3045011.97

One or more components have overridden mass properties:

Frame Bottom<1><Default>

Short Spacer<1><Default>

Short Spacer<2><Default>

Short Spacer<3><Default>

Short Spacer<4><Default>

Short Spacer<5><Default>

Short Spacer<6><Default>

Short Spacer<7><Default>

Short Spacer<8><Default>

Short Spacer<9><Default>

Short Spacer<10><Default>

Short Spacer<11><Default>

Short Spacer<12><Default>

Short Spacer<13><Default>

Short Spacer<14><Default>

Short Spacer<15><Default>

Short Spacer<16><Default>

Short Spacer<17><Default>

Short Spacer<18><Default>

Short Spacer<19><Default>

Short Spacer<20><Default>

Short Spacer<21><Default>

Short Spacer<22><Default>

Short Spacer<23><Default>

Short Spacer<24><Default>

Frame Bottom<2><Default>

Top Plate<1><Default>@Top Assembly<1><Default>

Long Spacer<1><Default>@Top Assembly<1><Default>

Long Spacer<2><Default>@Top Assembly<1><Default>

Long Spacer<3><Default>@Top Assembly<1><Default>

Long Spacer<4><Default>@Top Assembly<1><Default>

Motor with Propeller<1><Default>

Arduino uno<1><Predeterminado>@Arduino Assembly<1><Default>

Battery<1><Default>

Leg<1><Default>

Leg<2><Default>

Leg<3><Default>

Leg<4><Default>

Motor with Propeller<5><Default>

Motor with Propeller<6><Default>

Motor with Propeller<7><Default>

Propeller Guard<1><Default>

Propeller Guard<2><Default>

Propeller Guard<3><Default>

Propeller Guard<4><Default>

# Mass Props with Blade Guards

Mass properties of FULL Assembly

Configuration: Default

Coordinate system: -- default --

Mass = 491.60 grams

Volume = 305080.41 cubic millimeters

Surface area = 204341.56 square millimeters

Center of mass: ( millimeters )

X = -0.04

Y = -5.59

Z = 0.02

Principal axes of inertia and principal moments of inertia: ( grams * square millimeters )

Taken at the center of mass.

Ix = ( 0.00, 0.00, 1.00) Px = 2623253.85

Iy = ( 1.00, 0.00, 0.00) Py = 2693637.60

Iz = ( 0.00, 1.00, 0.00) Pz = 4263586.37

Moments of inertia: ( grams * square millimeters )

Taken at the center of mass and aligned with the output coordinate system.

Lxx = 2693636.61 Lxy = -540.75 Lxz = -287.46

Lyx = -540.75 Lyy = 4263586.13 Lyz = 314.27

Lzx = -287.46 Lzy = 314.27 Lzz = 2623255.09

Moments of inertia: ( grams * square millimeters )

Taken at the output coordinate system.

Ixx = 2709000.60 Ixy = -439.70 Ixz = -287.87

Iyx = -439.70 Iyy = 4263587.04 Iyz = 252.04

Izx = -287.87 Izy = 252.04 Izz = 2638619.48

One or more components have overridden mass properties:

Frame Bottom<1><Default>

Short Spacer<1><Default>

Short Spacer<2><Default>

Short Spacer<3><Default>

Short Spacer<4><Default>

Short Spacer<5><Default>

Short Spacer<6><Default>

Short Spacer<7><Default>

Short Spacer<8><Default>

Short Spacer<9><Default>

Short Spacer<10><Default>

Short Spacer<11><Default>

Short Spacer<12><Default>

Short Spacer<13><Default>

Short Spacer<14><Default>

Short Spacer<15><Default>

Short Spacer<16><Default>

Short Spacer<17><Default>

Short Spacer<18><Default>

Short Spacer<19><Default>

Short Spacer<20><Default>

Short Spacer<21><Default>

Short Spacer<22><Default>

Short Spacer<23><Default>

Short Spacer<24><Default>

Frame Bottom<2><Default>

Top Plate<1><Default>@Top Assembly<1><Default>

Long Spacer<1><Default>@Top Assembly<1><Default>

Long Spacer<2><Default>@Top Assembly<1><Default>

Long Spacer<3><Default>@Top Assembly<1><Default>

Long Spacer<4><Default>@Top Assembly<1><Default>

Motor with Propeller<1><Default>

Arduino uno<1><Predeterminado>@Arduino Assembly<1><Default>

Battery<1><Default>

Leg<1><Default>

Leg<2><Default>

Leg<3><Default>

Leg<4><Default>

Motor with Propeller<5><Default>

Motor with Propeller<6><Default>

Motor with Propeller<7><Default>

Propeller Guard<1><Default>

Propeller Guard<2><Default>

Propeller Guard<3><Default>

Propeller Guard<4><Default>

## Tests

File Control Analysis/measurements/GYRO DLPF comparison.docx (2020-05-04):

# 184 Hz

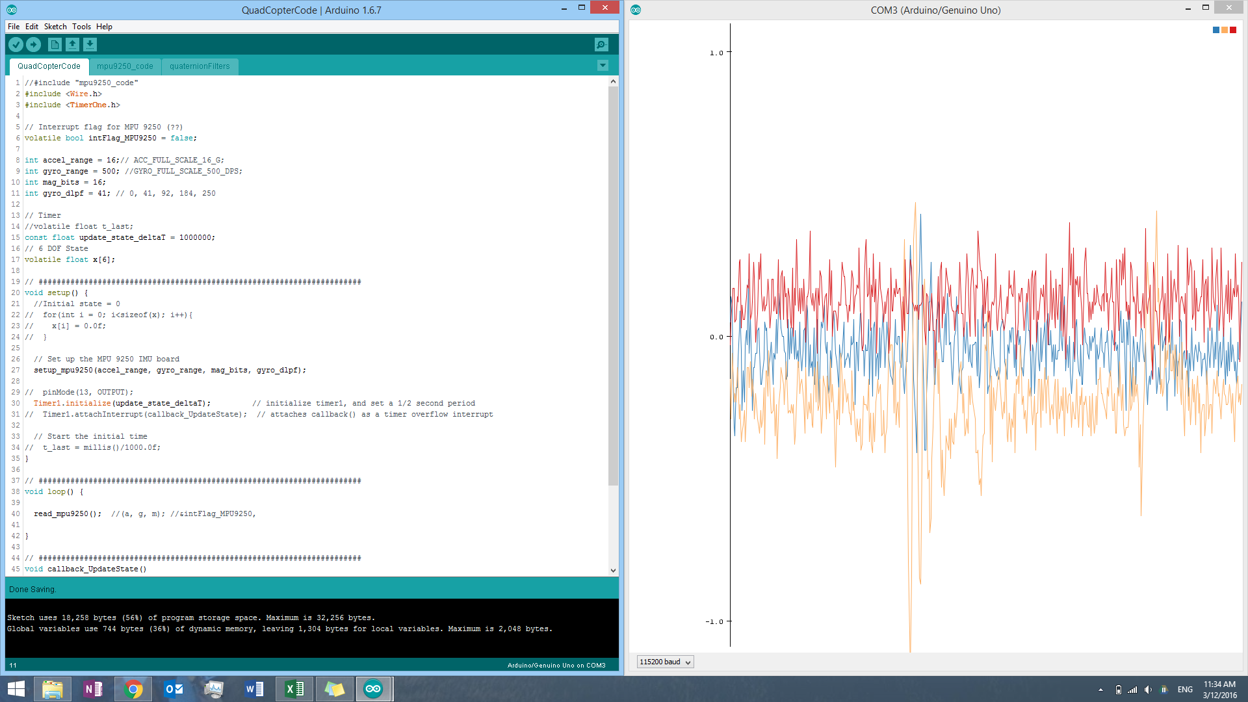
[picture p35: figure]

# 41 Hz

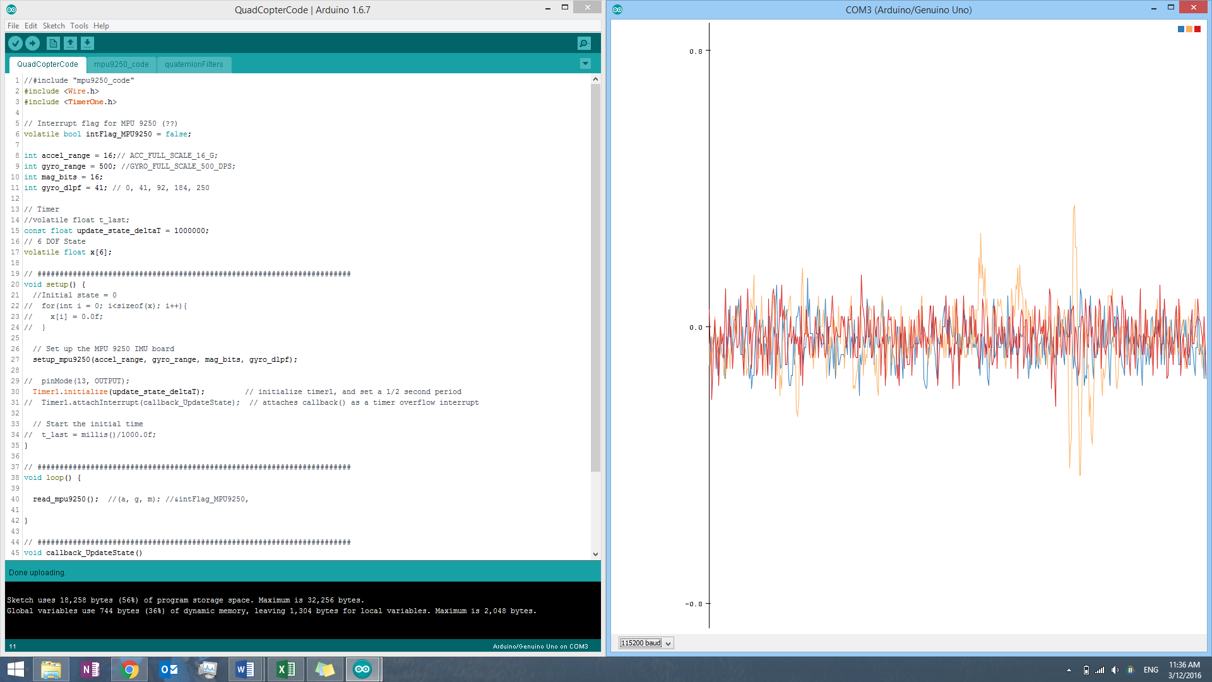
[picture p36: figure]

# No DLPF

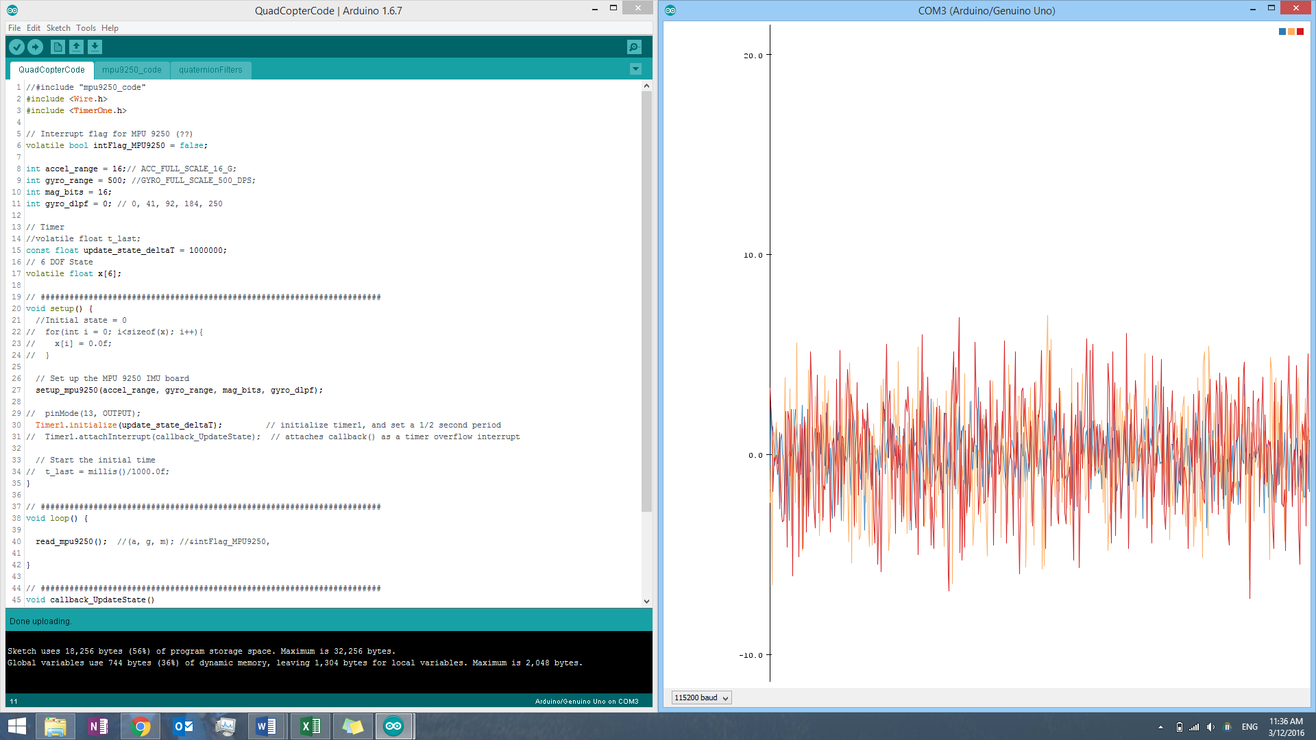
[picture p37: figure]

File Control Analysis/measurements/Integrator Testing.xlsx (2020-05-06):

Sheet: Sheet1
0 | -0.17 | 0 | 0.09 | 0.37
-0.06 | -0.12 | 0 | 0 | 0
-0.01 | -0.46 | 0 | 0 | 0
-0.1 | -0.09 | -0.01 | 0 | 0
-0.12 | -0.64 | -0.02 | 0 | 0
-0.12 | -0.35 | -0.03 | 0 | 0
-0.11 | -0.26 | -0.04 | 0 | 0
-0.12 | -0.43 | -0.05 | 0 | 0
-0.1 | -0.12 | -0.06 | 0 | 0
-0.09 | -0.56 | -0.07 | 0 | 0
-0.06 | -0.31 | -0.07 | 0 | 0
-0.06 | -0.11 | -0.08 | 0 | 0
-0.06 | -0.31 | -0.09 | 0 | 0
-0.05 | 0.03 | -0.09 | 0 | 0
-0.05 | -0.49 | -0.09 | 0 | 0
-0.04 | -0.03 | -0.1 | 0 | 0
-0.04 | -0.03 | -0.1 | 0 | 0
-0.01 | -0.17 | -0.1 | 0 | 0
-0.02 | 0.03 | -0.1 | 0 | 0
-0.02 | 0.08 | -0.1 | 0 | 0
0 | -0.24 | -0.1 | 0.16 | 0
-0.01 | -0.24 | -0.1 | 0 | 0
-0.01 | 0.05 | -0.1 | 0 | 0
-0.01 | -0.23 | -0.1 | 0 | 0
-0.01 | -0.43 | -0.1 | 0 | 0
-0.01 | -0.08 | -0.11 | 0 | 0
-0.01 | -0.46 | -0.11 | 0 | 0
-0.01 | -0.21 | -0.11 | 0 | 0
-0.01 | 0.72 | -0.11 | 0 | 0
-0.01 | 0.31 | -0.11 | 0 | 0
0 | -0.29 | -0.11 | 0 | 0
-0.01 | -0.6 | -0.11 | 0 | 0
-0.01 | 0.35 | -0.11 | 0 | 0
-0.01 | -0.49 | -0.11 | 0 | 0
0 | -0.14 | -0.11 | 0 | 0
-0.02 | -0.52 | -0.11 | 0 | 0
0 | 0.41 | -0.11 | 0 | 0
-0.01 | -0.81 | -0.12 | 0 | 0
-0.01 | -0.12 | -0.12 | 0 | 0
-0.01 | -0.26 | -0.12 | 0 | 0
-0.01 | -0.93 | -0.12 | 0 | 0
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

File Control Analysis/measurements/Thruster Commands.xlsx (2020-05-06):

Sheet: Sheet1
Project
QuadCopterCode
lib
EnableInterrupt
PinChangeInt
readme.txt
QuadCopterCode
controller.ino
mpu9250_code.ino
QuadCopterCode.ino
quaternionFilters.ino
readingSensors.ino
README.md
receiveRadioSignal.ino
stateEstimator.ino
.gitignore
.travis.yml
platformio.ini
1
2
3
4
5
6
#include <Arduino.h>
//#include <EnableInterrupt.h>
#include <PinChangeInt.h> //http://www.benripley.com/diy/arduino/three-ways-to-read-a-pwm-signal-with-arduino/
// #include <Average.h>
#define MAX_ANGLE_COMMAND 10
59 | 0 | 0.6 | 0 | -0.2 | | | -0.06 | -0.06 | | | -0.01 | 0 | | | 59.75 | 56.67 | 58.22 | 61.08
59 | 0 | -0.51 | 0 | 0.37 | | | -0.03 | -0.01 | | | 0.01 | -0.01 | | | 58.5 | 61.34 | 59.48 | 56.32
59 | 0 | 0 | 0 | 0.54 | | | -0.31 | -0.19 | | | 0.01 | -0.01 | | | 59.13 | 60.73 | 58.87 | 57.1
59 | 0 | 0.57 | 0 | -0.23 | | | -0.1 | 0.03 | | | -0.01 | 0 | | | 59.71 | 57.08 | 58.27 | 60.74
59 | 0 | -0.15 | 0 | -0.01 | | | -0.05 | 0 | | | 0 | 0 | | | 58.41 | 59.5 | 59.57 | 58.49
59 | 0 | 0.33 | 0 | -0.06 | | | -0.06 | 0 | | | 0 | 0 | | | 59.56 | 58.09 | 58.43 | 59.86
59 | 0 | 0.17 | 0 | 0.38 | | | -0.09 | 0.01 | | | 0 | -0.01 | | | 60.25 | 59.83 | 57.66 | 58.13
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

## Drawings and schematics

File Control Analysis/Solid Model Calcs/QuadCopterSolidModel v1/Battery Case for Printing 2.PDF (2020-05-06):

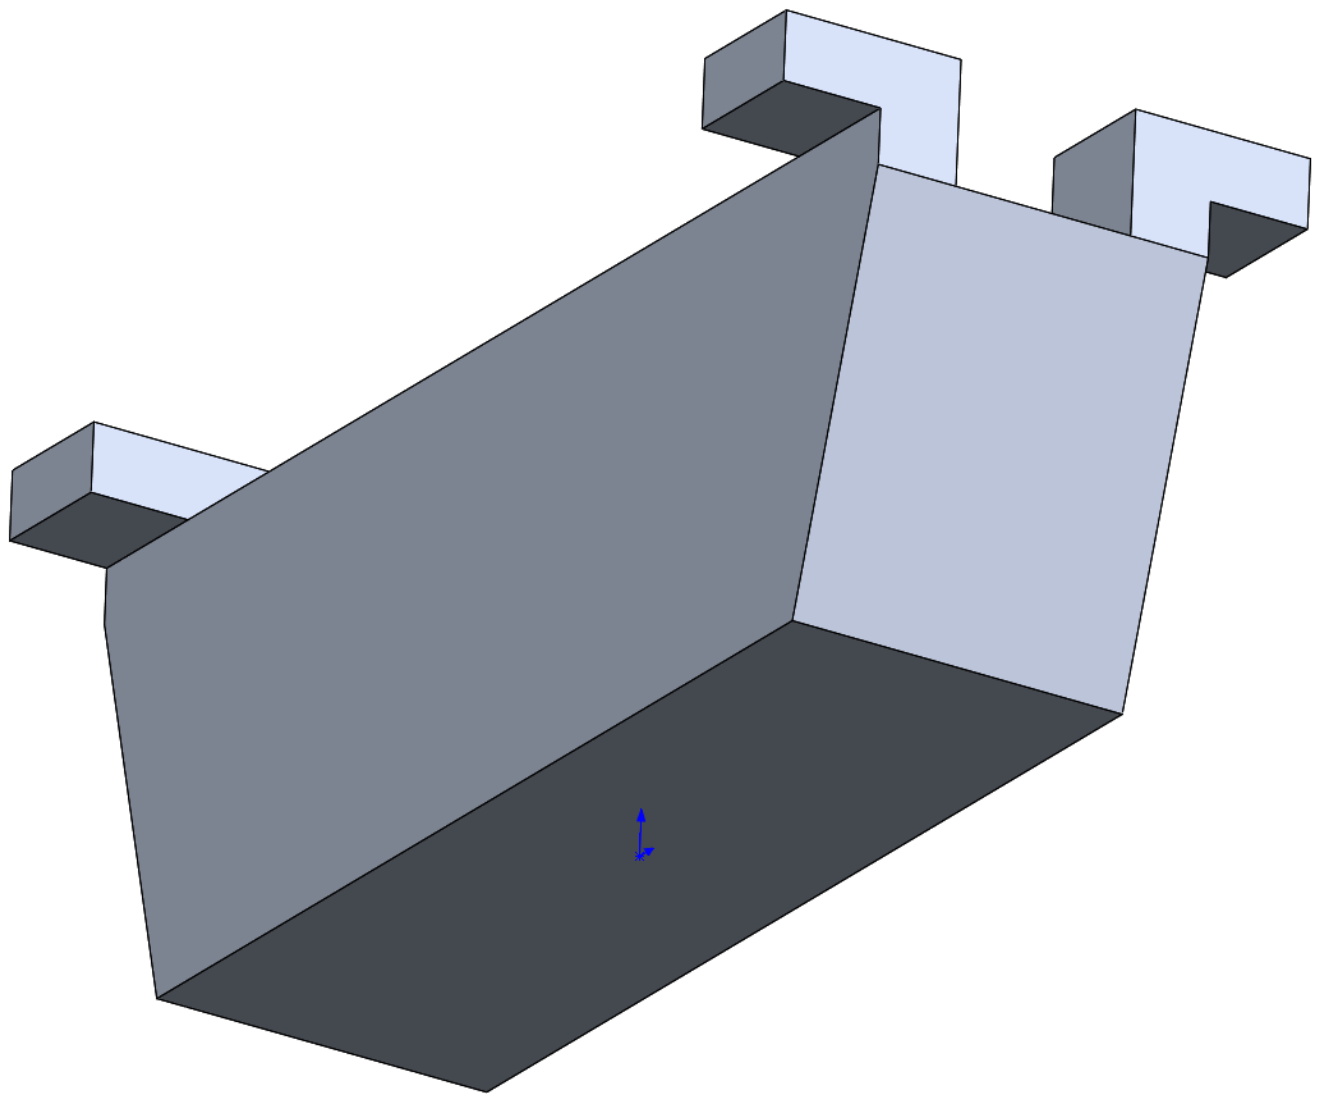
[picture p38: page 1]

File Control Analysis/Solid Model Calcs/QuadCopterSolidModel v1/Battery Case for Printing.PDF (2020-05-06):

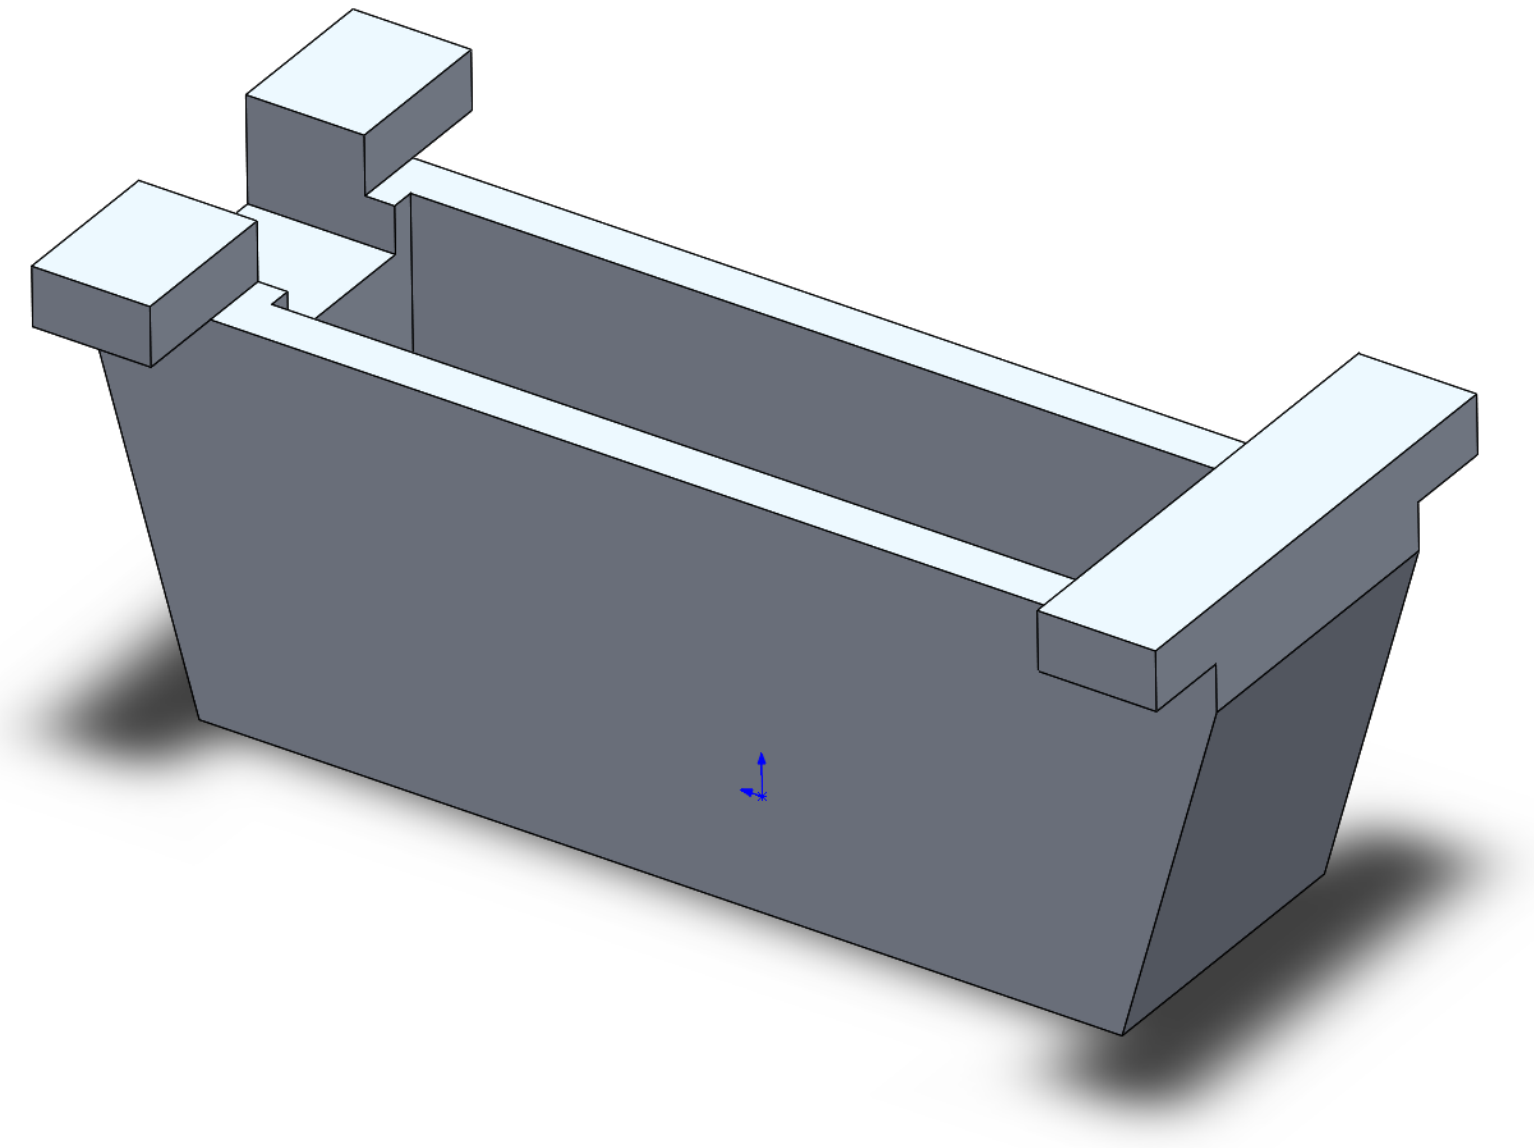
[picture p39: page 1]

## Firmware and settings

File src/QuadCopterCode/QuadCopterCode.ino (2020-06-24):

#include <Arduino.h>

#include <Wire.h>
// #include <TimerOne.h>
#include <Servo.h>
// #include <Plotter.h>

/**************************************************************
 * Pin outs for radio and LED indicator
**************************************************************/
#define LED_STABLE 8
// #define PIN_LEFT_STICK_LEFTRIGHT 8???
#define PIN_LEFT_STICK 9
#define PIN_RIGHT_STICK_UPDOWN 10
#define PIN_RIGHT_STICK_LEFTRIGHT 11
#define PIN_LEFT_KNOB 2
#define PIN_RIGHT_KNOB 5
#define NUM_PINS 12 // Number of potential input pins

Servo esc0;
Servo esc1;
Servo esc2;
Servo esc3;
float escControlVec[4];

// Interrupt flag for MPU 9250
volatile bool intFlag_MPU9250 = false;

int accel_range = 16; // ACC_FULL_SCALE_16_G;
int gyro_range = 500; // GYRO_FULL_SCALE_500_DPS;
int mag_bits = 16;
int gyro_dlpf = 41;  // 0, 41, 92, 184, 250
int accel_dlpf = 41; // 0, 41, 92, 184, 460

// Timer
// volatile float t_last;
const float update_state_deltaT = 1000000;
// Linear position
float x[3]; // x, y, z
// Linear velocity
float v[3];                            // vx, vy, vz
float euler_angles[3];                 // yaw, pitch, roll (3-2-1)
float a[3], g[3], m[3];                // variables to hold latest sensor data values
float q[4] = {1.0f, 0.0f, 0.0f, 0.0f}; // vector to hold quaternion
float eInt[3] = {
    0.0f, 0.0f,
    0.0f};                         // vector to hold integral error for estimator Mahony method
float integrated_pitch_err = 0.0f; // integral error for Controller
float integrated_roll_err = 0.0f;  // integral error for Controller
float delta_time = 0.0f;           // integration interval for both filter schemes

uint32_t lastUpdate =
    0;            //, firstUpdate = 0; // used to calculate integration interval
uint32_t Now = 0; // used to calculate integration interval

volatile float valLeftThrottle = 0;
volatile float valRightThrottleUpDown = 0;
volatile float valRightThrottleLeftRight = 0;

volatile unsigned long pwm_val = 0;
volatile unsigned long prev_times[NUM_PINS];
volatile float radioRecieverVals[NUM_PINS];
unsigned long minIns[NUM_PINS];
unsigned long maxIns[NUM_PINS];
int minOuts[NUM_PINS];
int maxOuts[NUM_PINS];
volatile unsigned long pwm_val_array[NUM_PINS];
unsigned long RADIO_STICK_DIFF = 370;
uint8_t latest_interrupted_pin;
int dumbCounter = 0;

const unsigned long timeout_limit = 100000;
const float DEG2RAD = PI /180.0f;

/**************************************************************
 * Function: setup
**************************************************************/
void setup()
{

    // Setup Serial Comms
    Serial.begin(115200);

    Serial.println("INITIALIZING...");

    // Setup motor control
    esc0.attach(A0); // setup esc0 on pin X
    esc1.attach(A1);
    esc2.attach(A2);
    esc3.attach(A3);

    // Initial State Variables
    for (int i = 0; i < 3; i++)
    {
        x[i] = 0.0f;
        v[i] = 0.0f;
        euler_angles[i] = 0.0f;
    }

    // Set up the MPU 9250 IMU board
    setup_mpu9250(accel_range, gyro_range, mag_bits, gyro_dlpf, accel_dlpf);

    // Set up the radio reciever
    // setupRadioReceiver();

    pinMode(LED_STABLE, OUTPUT);

    // set integration time by time elapsed since last filter update
    Now = micros();
    delta_time = ((Now - lastUpdate) / 1000000.0f);
    lastUpdate = Now;

    // while (millis() < 1000)
    // {
    //     Serial.println("Testing!!!");
    //     read_mpu9250();
    //     updateState();
    // }

    Serial.print("Initial Pitch = ");
    Serial.println(euler_angles[1]);
    Serial.print("Initial Roll = ");
    Serial.println(euler_angles[2]);
    // while(abs(euler_angles[1])>2.0){
    //   read_mpu9250();
    //   updateState();
    //   Serial.print("Waiting on PITCH to stabilize: ");
    //   Serial.println(euler_angles[1]);
    // }
    // while(abs(euler_angles[2])>2.0){
    //   read_mpu9250();
    //   updateState();
    //   Serial.print("Waiting on ROLL to stabilize: ");
    //   Serial.println(euler_angles[2]);
    // }
    Serial.println("--------------------------------------------------");
    Serial.println("*** PITCH and ROLL have stabilized! ***");
    Serial.print("Pitch = ");
    Serial.println(euler_angles[1]);
    Serial.print("Roll = ");
    Serial.println(euler_angles[2]);
    Serial.println("--------------------------------------------------");

}

/**************************************************************
 * Function: loop
**************************************************************/
void loop()
{
    Serial.println("Loop!");
    delay(500);

    read_mpu9250();
    updateState();

    // readRecieverData();
    // delay(50);

    // calculateControlVector();

    // esc0.write(escControlVec[0]);
    // esc1.write(escControlVec[1]);
    // esc2.write(escControlVec[2]);
    // esc3.write(escControlVec[3]);

}

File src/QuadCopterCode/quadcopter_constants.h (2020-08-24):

#include <Arduino.h>

#ifndef QUADCOPTER_CONSTANTS_H
#define QUADCOPTER_CONSTANTS_H

#define PIN_LED_LEVEL_INDICATOR 8 // pin to light LED if level

#define NUM_PINS 12  // Number of potential input pins
#define NUM_INPUTS 5 // Number of actually used inputs for radio

#define PIN_LEFT_STICK 9
#define INDEX_LEFT_STICK 2

#define PIN_RIGHT_STICK_UPDOWN 10
#define INDEX_RIGHT_STICK_UPDOWN 3

#define PIN_RIGHT_STICK_LEFTRIGHT 11
#define INDEX_RIGHT_STICK_LEFTRIGHT 4

#define PIN_LEFT_KNOB 2 // something's off with this
#define INDEX_LEFT_KNOB 0

#define PIN_RIGHT_KNOB 5
#define INDEX_RIGHT_KNOB 1

static const float DEG2RAD = PI / 180.0f;

#endif

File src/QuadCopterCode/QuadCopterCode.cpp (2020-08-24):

#include <Arduino.h>
#include <controller.h>
#include <Wire.h>
#include <Servo.h>
#include <mpu9250_code.h>
#include <state_estimator.h>
#include <quadcopter_constants.h>
#include <global_junk.h>
#include <receive_radio_signal.h>
#include <serial_printing.h>

/**************************************************************
 * Pin outs for radio and LED indicator
**************************************************************/
Servo motor0;
Servo motor1;
Servo motor2;
Servo motor3;
float motor_control_vector[4];

// Interrupt flag for MPU 9250
volatile bool interrupt_flag_MPU9250 = false;
bool is_initializing = true;

// Timer
uint32_t last_update_microseconds = 0; // used to calculate integration interval
float euler_angles[3];                 // yaw, pitch, roll (3-2-1)

float quaternion_vector[4] = {1.0f, 0.0f, 0.0f, 0.0f}; // vector to hold quaternion

// initialize global junk
volatile unsigned long last_rise_time[NUM_INPUTS];
volatile float input_radio_values[NUM_INPUTS];

/**************************************************************
 * Function: EstimateStateAndControlVec
**************************************************************/
inline void EstimateStateAndControlVec()
{

    float accel_vector_xyz[3], g[3], magnetometer_vector[3]; // variables to hold latest sensor data values

    // integration interval for both filter schemes
    const uint32_t now_microseconds = micros();
    float delta_time_sec = ((now_microseconds - last_update_microseconds) / 1000000.0f); // set integration time by time elapsed since last filter update
    last_update_microseconds = now_microseconds;

    ReadMPU9250(accel_vector_xyz, g, magnetometer_vector);
    UpdateState(accel_vector_xyz, g, magnetometer_vector, quaternion_vector, delta_time_sec, euler_angles);

    CalculateControlVector(euler_angles, g, motor_control_vector, delta_time_sec);
}

/**************************************************************
 * Function: setup
**************************************************************/
void setup()
{

    // Setup Serial Comms
    Serial.begin(115200);

    Serial.println(F("INITIALIZING..."));

    // Setup motor control
    motor0.attach(A0);
    motor1.attach(A1);
    motor2.attach(A2);
    motor3.attach(A3);

    // Set up the MPU 9250 IMU board
    SetupMPU9250();

    // Set up the radio reciever
    SetupRadioReceiver(input_radio_values);

    pinMode(PIN_LED_LEVEL_INDICATOR, OUTPUT);

    EstimateStateAndControlVec();
    Serial.print(F("Initial Pitch = "));
    Serial.println(euler_angles[1]);
    Serial.print(F("Initial Roll = "));
    Serial.println(euler_angles[2]);
    while (abs(euler_angles[1]) > 2.0)
    {
        EstimateStateAndControlVec();
        // Serial.print("Waiting on PITCH to stabilize: ");
        // Serial.println(euler_angles[1]);
    }
    while (abs(euler_angles[2]) > 2.0)
    {
        EstimateStateAndControlVec();
        // Serial.print("Waiting on ROLL to stabilize: ");
        // Serial.println(euler_angles[2]);
    }
    Serial.println(F("--------------------------------------------------"));
    Serial.println(F("*** PITCH and ROLL have stabilized! ***"));
    Serial.print(F("Pitch = "));
    Serial.println(euler_angles[1]);
    Serial.print(F("Roll = "));
    Serial.println(euler_angles[2]);
    Serial.println(F("--------------------------------------------------"));
}

/**************************************************************
 * Function: loop
**************************************************************/
void loop()
{
    EstimateStateAndControlVec();

    // Serial.print("|");
    // Serial.print(radioRecieverVals[0]);
    // Serial.print("\t");
    // Serial.print(radioRecieverVals[1]);
    // Serial.print("\t");
    // Serial.print(radioRecieverVals[2]);
    // Serial.print("\t");
    // Serial.print(radioRecieverVals[3]);
    // Serial.print("\t");
    // Serial.print(radioRecieverVals[4]);

    motor0.write(motor_control_vector[0]);
    motor1.write(motor_control_vector[1]);
    motor2.write(motor_control_vector[2]);
    motor3.write(motor_control_vector[3]);
}

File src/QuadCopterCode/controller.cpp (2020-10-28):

#include <Arduino.h>
#include <quadcopter_constants.h>
#include <controller.h>
#include <global_junk.h>
#include <serial_printing.h>

/**************************************************************
 * Variables
**************************************************************/
byte dumb_counter = 0;
float integrated_pitch_err_rad = 0.0f; // integral error for Controller
float integrated_roll_err_rad = 0.0f;  // integral error for Controller

/**************************************************************
 * Function: thrustToMotorValLinear
**************************************************************/
float thrustToMotorValLinear(float delta_thrust, float val0)
{
    // max RPM of 14618 (go from 0 to max if throttle from 40 to 180)
    const float rpm2val = (180.0 - 40.0) / (14618.0 - 0.0);
    const float thrust2rpm = (14618.0 - 0.0) / (3.5 - 0);
    // float deltaOmega;
    // // float omega0 = max(val0,40)/rpm2val;
    // float omega0 = max(map(val0, 40.0, 180.0, 0.0, 14600.0),1000);
    // //Serial.print(omega0); Serial.print(F("\t"));
    // deltaOmega = deltaThrust/(2*omega0*18.00201E-09);
    // // deltaOmega = deltaThrust/(2*omega0*9.00201E-09);
    //
    // return deltaOmega*rpm2val;
    return delta_thrust * thrust2rpm * rpm2val;
}

// ---------- Nonlinear transformation from desired force to motor command val ------------
const float nMinimumValue = -20.0;
const float nLinearToQuadtraicTransition = 40.0; // value at which the curve-fit transitions from linear to quadratic
const float nForceAtLinearToQuadratic = 0.10;    // pseudo-force when motors are driven with a value at the switch from linear to quadratic
const float nLinearSlope = (3.5 - nForceAtLinearToQuadratic) / ((180.0 - nLinearToQuadtraicTransition) * (180.0 - nLinearToQuadtraicTransition));

/**************************************************************
 * Function: motorValToThrustNonlinear
**************************************************************/
float motorValToThrustNonlinear(float val0)
{
    if (val0 > nLinearToQuadtraicTransition)
    {
        return nLinearSlope * (val0 - nLinearToQuadtraicTransition) * (val0 - nLinearToQuadtraicTransition) + nForceAtLinearToQuadratic;
    }
    else
    {
        return (val0 - nMinimumValue) * nForceAtLinearToQuadratic / (nLinearToQuadtraicTransition - nMinimumValue);
    }
}

/**************************************************************
 * Function: thrustToMotorValNonlinear
**************************************************************/
float thrustToMotorValNonlinear(float delta_thrust, float val0)
{
    float thrust = max(0, delta_thrust + motorValToThrustNonlinear(val0));
    float motor_val_out;

    if (thrust > nForceAtLinearToQuadratic)
    {
        // quadratic portion of curve
        motor_val_out = sqrt((thrust - nForceAtLinearToQuadratic) / nLinearSlope) + nLinearToQuadtraicTransition;
    }
    else
    {
        // linear regime of fit curve
        motor_val_out = thrust / (nForceAtLinearToQuadratic / (nLinearToQuadtraicTransition - nMinimumValue)) + nMinimumValue;
    }

    return constrain(motor_val_out, 0.0, 180.0);
}

/**************************************************************
 * Function: calculateControlVector
**************************************************************/
void CalculateControlVector(float *euler_angles, float *angular_rates_deg, float *motor_control_vector, float delta_time_sec)
{
    // ----------- LQR state gains -----------
    // // Derivitive feedback term
    // const float kD = 0.243/4.0; //3.43; //0.1114; //0.1431; //0.0385; //0.01;
    // // Propoortional feedback term
    // const float kP = 4.243/4.0;//6.83;// 0.9487;//1.5652;// 0.1118; //0.3;
    // // Reference adjustment
    // const float Nbar = kP; //0.1118;
    // ---------------------------------------

    // ----------- PD/PID state gains -----------
    // const float kD = 0.04769*2*radioRecieverVals[INDEX_LEFT_KNOB]/100.0; // Derivitive feedback term
    // const float kP = 0.6212*2*radioRecieverVals[INDEX_LEFT_KNOB]/100.0;// Propoortional feedback term
    // const float kP = 0.07;  //*radioRecieverVals[INDEX_LEFT_KNOB]/100.0;// Propoortional feedback term
    // const float kI = 0.55;  // Integral feedback term
    // const float kD = 0.055; // *radioRecieverVals[INDEX_LEFT_KNOB]/100.0; // Derivitive feedback term

    // From Xcos simulation
    const float kP = 0.05;
    const float kI = 0.015;
    const float kD = 0.02;

    // Reference adjustment
    // const float Nbar = kP; //0.1118;
    // ---------------------------------------

    float delta_force_pitch;
    float delta_force_roll;
    float pitch_err_rad = 0.0;
    float roll_err_rad = 0.0;

    // // use Euler angles to calculate errors only if within certain range
    if ((abs(euler_angles[1]) < 85) && (abs(euler_angles[2]) < 85))
    {

        // Only send commands to the motor if recieving a radio signal
        // This provides a nice remote kill switch
        if (checkForActiveSignal())
        {

            if (is_initializing)
            {
                // if we're initializing, just send the raw left throttle
                motor_control_vector[0] = thrustToMotorValNonlinear(0, input_radio_values[INDEX_LEFT_STICK]);
                motor_control_vector[2] = thrustToMotorValNonlinear(0, input_radio_values[INDEX_LEFT_STICK]);
                motor_control_vector[1] = thrustToMotorValNonlinear(0, input_radio_values[INDEX_LEFT_STICK]);
                motor_control_vector[3] = thrustToMotorValNonlinear(0, input_radio_values[INDEX_LEFT_STICK]);
            }
            else
            {

                // TODO: move each control approach into its own function
                // --- LQR Controller design ---
                // u = Nbar*r - K*x
                // deltaF_pitch = (radioRecieverVals[INDEX_RIGHT_STICK_UPDOWN]*Nbar - pitch*kP)*DEG2RAD + (0.0f*Nbar - pitch_rate*kD)*DEG2RAD;
                // deltaF_roll = (radioRecieverVals[INDEX_RIGHT_STICK_LEFTRIGHT]*Nbar - roll*kP)*DEG2RAD + (0.0f*Nbar - roll_rate*kD)*DEG2RAD;
                // ------------------------------

                // --- PID Controller design w/ integrator limit ---
                // scale_val = min(1.0, (input_left_throttle / 100.0) * (input_left_throttle / 100.0));
                pitch_err_rad = (-input_radio_values[INDEX_RIGHT_STICK_UPDOWN] - euler_angles[2]) * DEG2RAD;
                roll_err_rad = (input_radio_values[INDEX_RIGHT_STICK_LEFTRIGHT] - euler_angles[1]) * DEG2RAD;

                // Only accrue integrator error once we're flying (so it doesn't ratchet up on the ground)
                if (input_radio_values[INDEX_LEFT_STICK] > 70)
                {
                    integrated_pitch_err_rad = constrain(integrated_pitch_err_rad * 0.999 + (pitch_err_rad * delta_time_sec), -0.25, 0.25);
                    integrated_roll_err_rad = constrain(integrated_roll_err_rad * 0.999 + (roll_err_rad * delta_time_sec), -0.25, 0.25);
                }
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

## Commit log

2016-02-12 setup() allows setting of gyro and accel ranges
2016-02-13 Sensor reading works now
    Changed MPU9250_ADDRESS to accurately read from board.
    Reduced number of global vars
2016-02-15 Revert "Sensor reading works now"
    This reverts commit 0ccf57220fee1229296a380bd0441b4230e91059.
    Conflicts:
    mpu9250_code.ino
    You are currently reverting commit 0ccf572.
    Changes to be committed:
    modified: mpu9250_code.ino
    [mpu9250_code.ino]
2016-02-16 Revert "Revert "Sensor reading works now""
    This reverts commit ae0ded4833b5ba6f5704d13392caad0baabf0bc9.
    [mpu9250_code.ino]
2016-02-16 Accelerometer giving correct values now
    It now returns values in m^2/s
    [QuadCopterCode.ino, mpu9250_code.ino]
2016-02-16 Accelerometer biases accurately calculated and used
2016-02-16 Better accelerometer bias removal
2016-02-17 Accurate accelerometer bias implementation
2016-02-19 Increased gyro sample rate
2016-03-13 Digital Low-Pass Filter Setup
    Set up the ability to control the bandwidth of the digital low-pass
    filter from the main code
2016-03-13 Better passing of sensor range/resolution commands
    Replaced all those global variables with local variables passed from
    function to function
    [mpu9250_code.ino]
2016-04-18 Semi-working Adjust Accelerometer
2016-10-25 Reading data from radio and controlling motors
    Now it can ready a signal from the radio reciever and control 4 motors!
2017-01-20 Added function to print 4-elem array
2017-03-12 Atom Update + Better Safeguards
    Now the code can be developed using Atom (new filestructure) and I added
    some safeguards to the controller so it doesn't go crazy when the
    quadcopter flips upside down.
    [QuadCopterCode.ino, mpu9250_code.ino, quaternionFilters.ino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]
2017-07-19 Added library files for enabling interrupts and pin changes
2017-10-28 LQR controller with nonlinear force-to-motor control
2017-10-28 Waiting for pitch and roll to stabilize before initiating control
    [QuadCopterCode.ino]
2020-05-04 Reorganizing code pics and docs before going to windows 10, random format updates too
    [Magnetometer Calibration Data.xlsx]
2020-05-06 Merging in docs from other locations, trying to undo add of massive media files
    [Arduino Assembly.SLDASM, Arduino proto shield R3.SLDPRT, Arduino uno.SLDPRT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]
2020-07-10 Fixing bug in degree to radio conversion; Removing loop print statementl
    [QuadCopterCode.cpp]
2020-07-21 YEEEEESSSSSS! Finally fixed the issue causing sporadic arduino resets/crashes (bad index on falling/rising interrupt attachments); also some misc variable renaming;
    [QuadCopterCode.cpp, controller.cpp, receive_radio_signal.cpp]
2020-08-01 Tuning state estimator gains and switching to Magdwick algorithm
2020-08-02 Some variable naming updates; fixing bug with showing radio val in controller;
    [QuadCopterCode.cpp, controller.cpp, quadcopter_constants.h]
2020-08-09 Calculating roll and pitch error even if controller off (but not integrating); not commanding motors if outside +/-85deg;
    [controller.cpp]
2020-08-10 First cut at detecting average radio receiver vals on startup (needs work)
2020-08-18 Using an exponential weighted average to get average radio signal; Radio init is now counted based off of number of calibrations (not pitch/roll stabilization) to avoid overflow if radio off when sta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
    [QuadCopterCode.cpp, controller.cpp, receive_radio_signal.cpp]
2020-08-18 Fixed a bug with INDEX vs PIN access index; hooking up motor commands (motor mapping still not tested)
    [QuadCopterCode.cpp, controller.cpp, receive_radio_signal.cpp]
2020-08-24 Removing some oddities in the controller; clarifying units on variables; fixing motor commands to correspond to the correct motor with new hardware setup; removing two unused globals; removed constan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
    [QuadCopterCode.cpp, controller.cpp, quadcopter_constants.h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]
2020-08-24 Changing coefficients in thrust curve fit
2020-09-11 Adding xcos simultion; organizing control analysis better
    [Controller Data - with motors.xlsx, Controller Data1.xlsx, Controller Data2.xlsx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]
2020-09-11 Only keep integrator error when flying; Updating gains from xcos simulation;
    [ArduinoSamplingPeriod.xlsx]
